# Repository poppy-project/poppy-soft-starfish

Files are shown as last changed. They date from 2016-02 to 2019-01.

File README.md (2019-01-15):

# Poppy Soft Starfish

This soft robot intergrates flexible silicon parts that can be easily design and built at a very low cost (>1$). It make use of the [poppy-soft-connector](https://github.com/poppy-project/poppy-soft-connector).

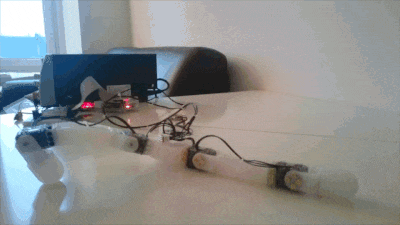
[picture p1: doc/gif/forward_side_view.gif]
forward_side_view


Discussions about this project are located at [this post](https://forum.poppy-project.org/t/poppy-soft-connector/2152). The project has been highlighted on [Hackaday](https://hackaday.com/2016/08/17/struggling-robot-made-with-diy-soft-limbs/)

## Principles 

By embedding hard connectors into silicon based parts, we create soft parts with a standard mechanical interface. These parts can be used as plug and play building blocks in our robots. See our [tutorial video](https://youtu.be/B3CZs55AJQo).

To create the soft part you have to prepare a mold of the desired shape. The mold's wall should be 2.2mm thick (for Ollo rivets) and include Ollo holes at the position you would like to add the connectors. The connectors are then positioned into the mold and maintained in place using Ollo rivet. You can then pour the polymer of your choice into the mold and allow for enough time for the polymer to cure - thus embedding the connector into the part. The soft part can then be unmolded and attached with XL-320 motors or any Ollo parts to create 'soft robots'. The starfish robot demonstrates how to use soft connectors.

The possibilities are immense as many different kinds of polymer can be used with many different properties. It also allows to embed electronics, sensors, cables, and more into the body of our robots. We hope this will tickle the imagination and open new possibilities for artistic minded people!

## More information

- [Tutorial video](https://youtu.be/B3CZs55AJQo)
- [doc folder](doc) for building instructions and help
- [hardware folder](hardware) for the mechanical parts
- [software folder](software) for code examples

### Contributing

Create your own soft robot and share it on [our forum](https://forum.poppy-project.org/)!

You can also propose new optimized design for the [poppy-soft-connector](https://github.com/poppy-project/poppy-soft-connector).

To contribute to this repository, you can [fork it](https://help.github.com/articles/fork-a-repo/) and issue a [pull request](https://help.github.com/articles/using-pull-requests/). [[Another useful link]](https://gun.io/blog/how-to-github-fork-branch-and-pull-request/)

### License

All the technological development work made in the Poppy project is freely available under open source licenses. Only the name usage *"Poppy"* is restricted and protected as an international trademark, please contact us if you want to use it or have more information.

| License | Hardware | Software |
| --- | :---: | :---: |
| Title  | [Creatives Commons BY-SA](http://creativecommons.org/licenses/by-sa/4.0/)  |[GPL v3](http://www.gnu.org/licenses/gpl.html)  |
| Logo  |   |GPL V3 (http://www.gnu.org/licenses/gpl.html)  |

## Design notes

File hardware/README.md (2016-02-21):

## Hardware

The parts have been design using [onshape](https://www.onshape.com/). The project has been made public at [this link](https://cad.onshape.com/documents/56af95b6e4b06a92e0eda720/w/a53eaed345df8e54532db1e2/e/a165c83ad81843f33ed38c05)
(Note: If the link does not work, run a search for ''Poppy Soft Robot XL320'')

The stl files are also available under [molds](molds) and [parts](parts).

Checkout the [BOM](BOM.md) to know how many of each to print.

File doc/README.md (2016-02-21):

## Building your robot

The complete bill of material is [here](BOM.md)

Video showcasing the building process are available:

- [Summary of all steps](https://youtu.be/B3CZs55AJQo)

- [Assembling the molds](https://youtu.be/NGw_e99sHJw)

- [Molding](https://youtu.be/pZrcofLqdRw)

- [Unmolding](https://youtu.be/WqsFyHN0t-A)

- [Assembling the robot](https://youtu.be/N8gOX-NB1fE)

Some demo code is available under the [software folder](https://github.com/poppy-project/poppy-soft-starfish/tree/master/software/poppy_soft_starfish), it implements the forward motion.

[[video_1]](https://youtu.be/_0Psq-BkSfY) [[video_2]](https://youtu.be/mUjL1PCE9o8) [[video_3]](https://youtu.be/N8iv0Vt9XzM)

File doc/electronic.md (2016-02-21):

# About the electronic

A small bit of electronic hacking is required for now. The cables between motors have two purposes:
- distribute alimentation to each motor
- convey messages to each motor (ordering them to move or asking them for sensors' values)

First, you will need a hub for connecting all arms together on the same communication and power bus.

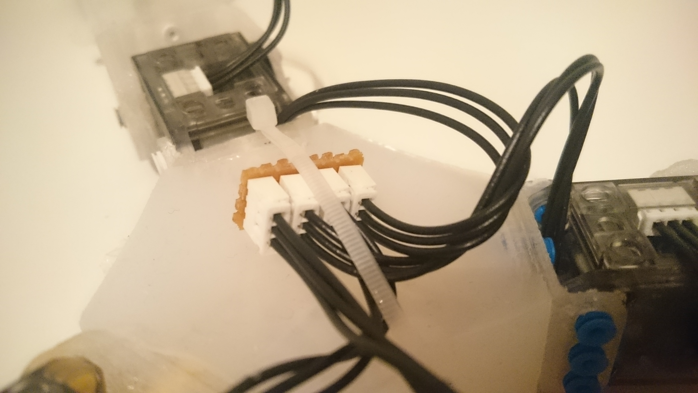
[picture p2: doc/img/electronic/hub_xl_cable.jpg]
Hub


Then you need to power the Xl320 motors with 7.5V. Thus the alimentation should be added between the USB2Dynamixel (that deals with communication aspects) and the motors. To this end simply create the following hack.

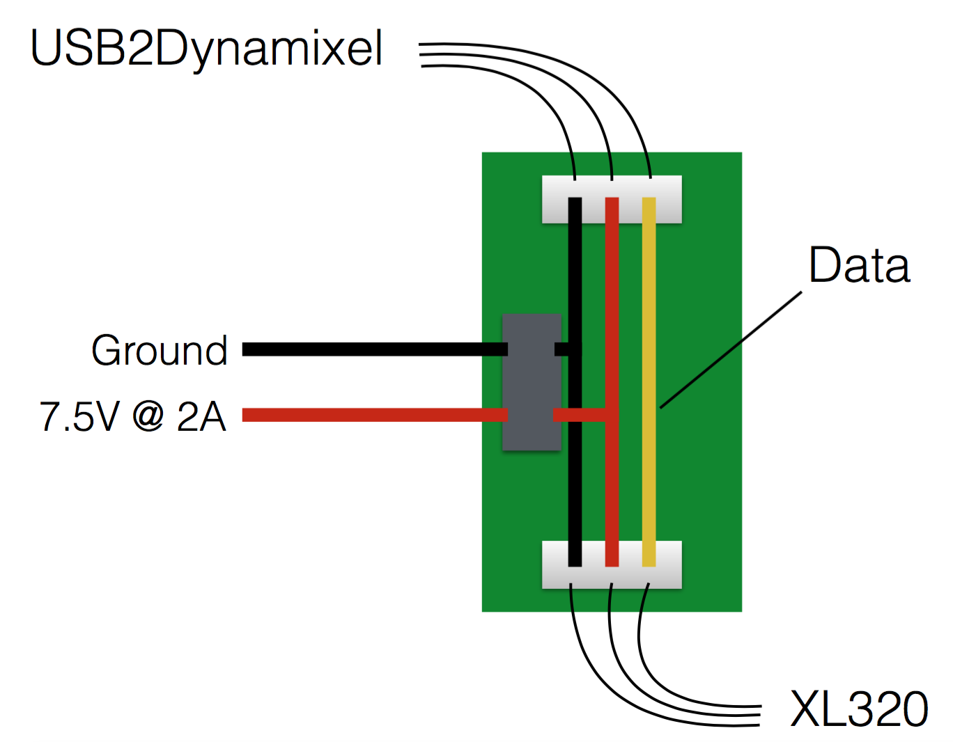
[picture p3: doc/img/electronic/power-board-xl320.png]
Power Board


Then connect the USB2Dynamixel on one end and the first motor on the other end. Connect the USB2Dynamixel to your computer or Raspberry Pi. And power the board with 7.5V.

The communication with the motor is TTL, thus configure the USB2Dynamixel in TTL mode as shown below.

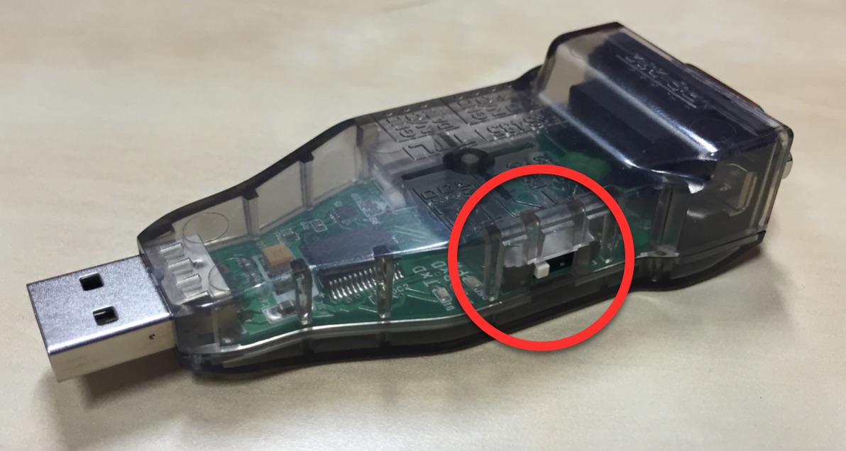
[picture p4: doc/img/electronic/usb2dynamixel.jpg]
USB2Dynamixel


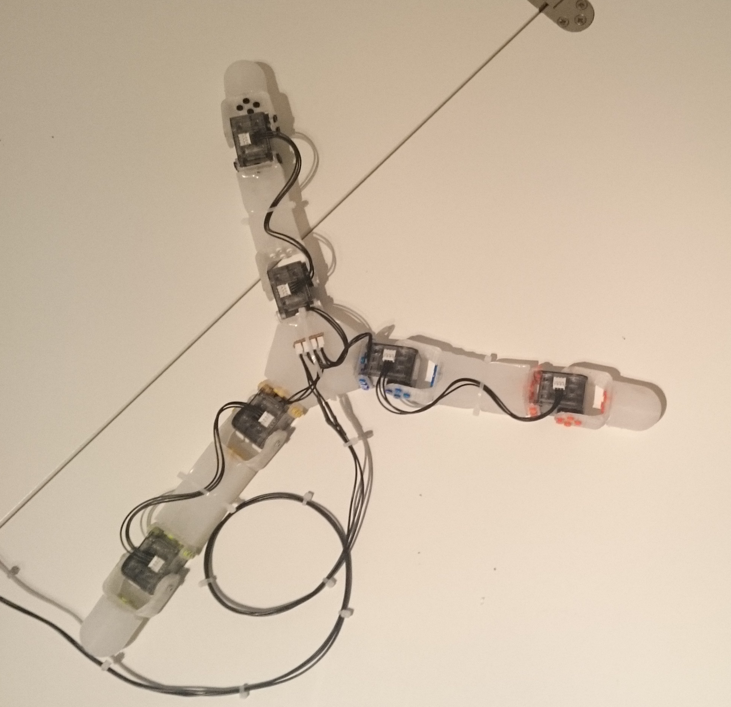
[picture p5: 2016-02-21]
doc/img/full_robot.jpg

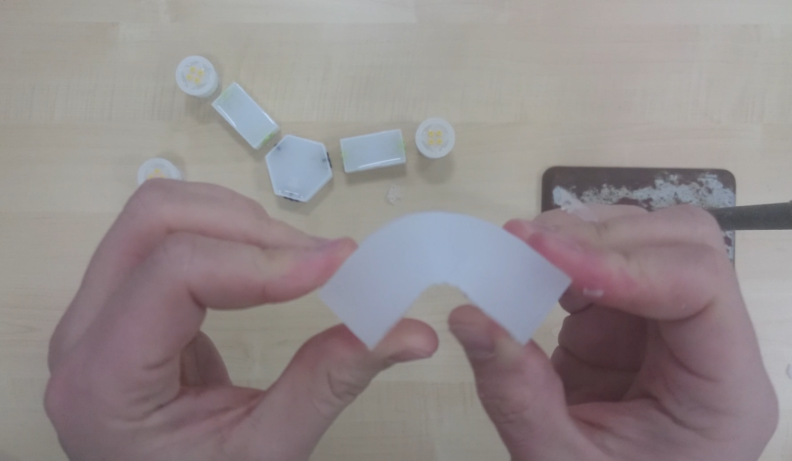
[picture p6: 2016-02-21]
doc/img/unmold.png

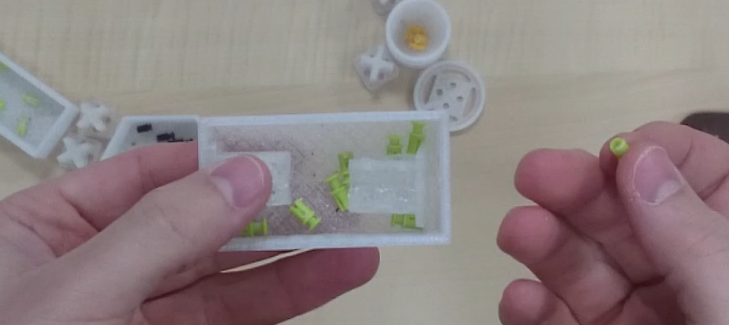
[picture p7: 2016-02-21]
doc/img/prepare_mold.png

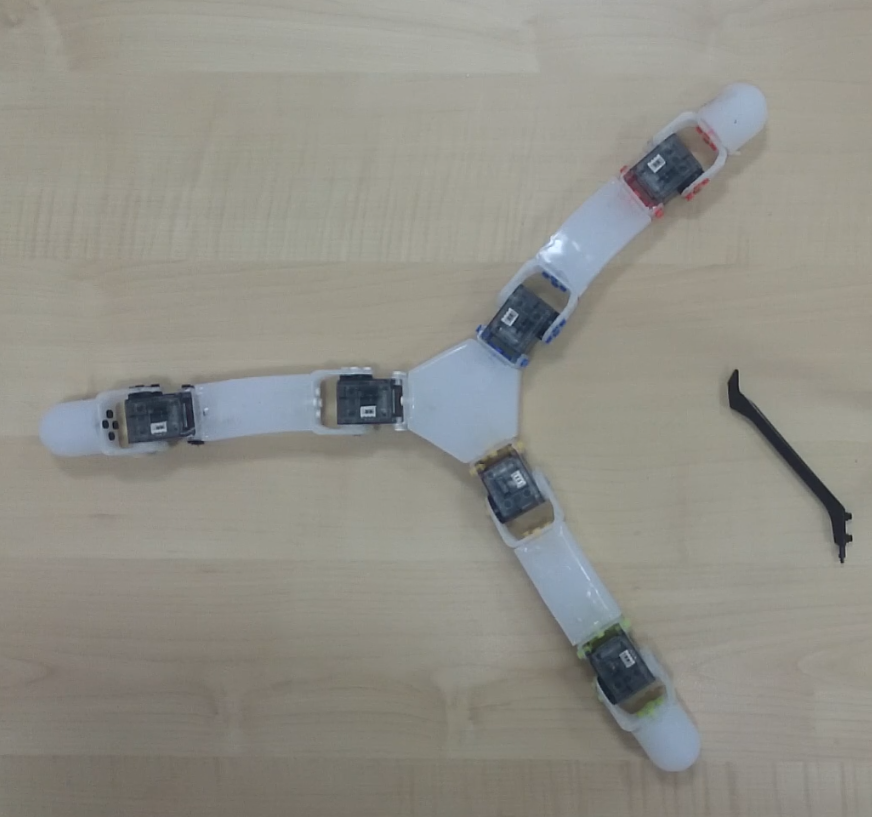
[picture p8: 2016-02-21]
doc/img/built.png

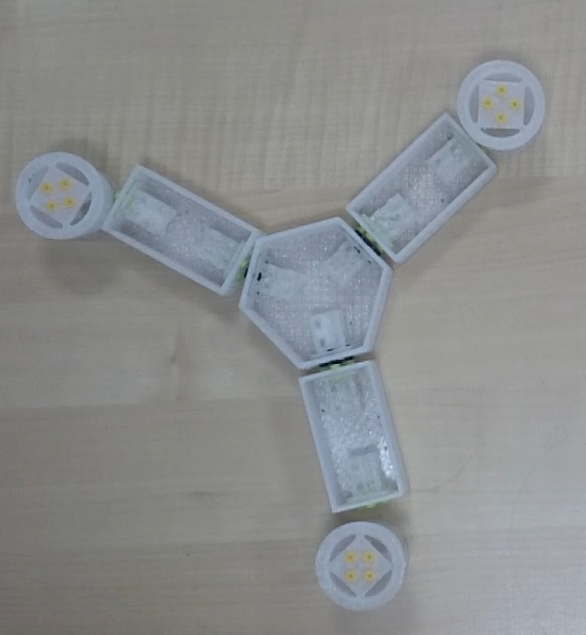
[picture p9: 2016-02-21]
doc/img/mold_ready.png

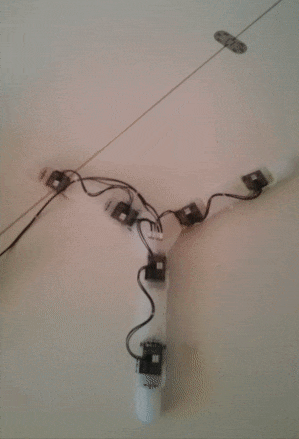
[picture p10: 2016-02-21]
doc/gif/forward_top_view.gif

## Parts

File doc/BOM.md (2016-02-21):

## BOM

For building a Poppy Soft Starfish, you will need:

* the 3D printed parts: [[STL]](https://github.com/poppy-project/poppy-soft-starfish/tree/master/hardware) [[BOM]](https://github.com/poppy-project/poppy-soft-starfish/blob/master/hardware/BOM.md)

* some silicone, we used the [Ecoflex 00-30](http://www.smooth-on.com/Silicone-Rubber-an/c2_1115_1130/index.html)

* 6x Robotis [XL-320](http://www.generationrobots.com/en/401692-dynamixel-xl-320-servo-motor.html?search_query=OLLO&results=23)
* 7x [XL cables](http://www.generationrobots.com/en/402091-3p-190-mm-cables-for-xl-servos-x5.html) (of which 1 longer for connecting to the electronics and allow some movement)

* many [OLLO rivets](http://www.generationrobots.com/en/401870-ollo-rivet-set-ors-10.html) (between 4 and 12 per motor)
* 1x [OLLO Tool](http://www.generationrobots.com/en/401872-ollo-tool.html)

* 1x [Raspberry Pi 2](https://www.raspberrypi.org/raspberry-pi-2-on-sale/) with its power supply

* 1x [USB2Dynamixel](http://www.generationrobots.com/en/400848-usb2dynamixel-robotis.html?search_query=usb2dynamixel&results=20)

* 1x [TTL cable](http://www.generationrobots.com/en/401739-3p-cable-set-bcs-3p01-for-dynamixel-servo-motors.html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)

* 1 external power supply able to output 7.5V at least 2A for the motors (see [here](https://forum.poppy-project.org/t/birth-of-poppyergojr-and-support-for-low-cost-xl-320-motors/1052/10) for details)

* 1x small electronic board (see the [electronic section](electronic.md))

* 1x 4 way hub for XL cables (see the [electronic section](electronic.md))

*All the links to products we provide are from our local distributor but feel free to choose your own.*

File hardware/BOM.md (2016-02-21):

## Molds

| Part Name | Quantity | Note |
| ---:|:---:|:---:|
| straight_large_mold | 3 |  |
| three_way_mold | 3 |  |
| feet_mold | 3 |  |
| feet_top_mold | 3 |  |

Depending on the time you have, one mold of each type is enough as they can be reused.

## Parts

| Part Name | Quantity | Note |
| ---:|:---:|:---:|
| soft_connector | 12 |  |
| short_U | 6 |  |
| long_U | 6 |  |

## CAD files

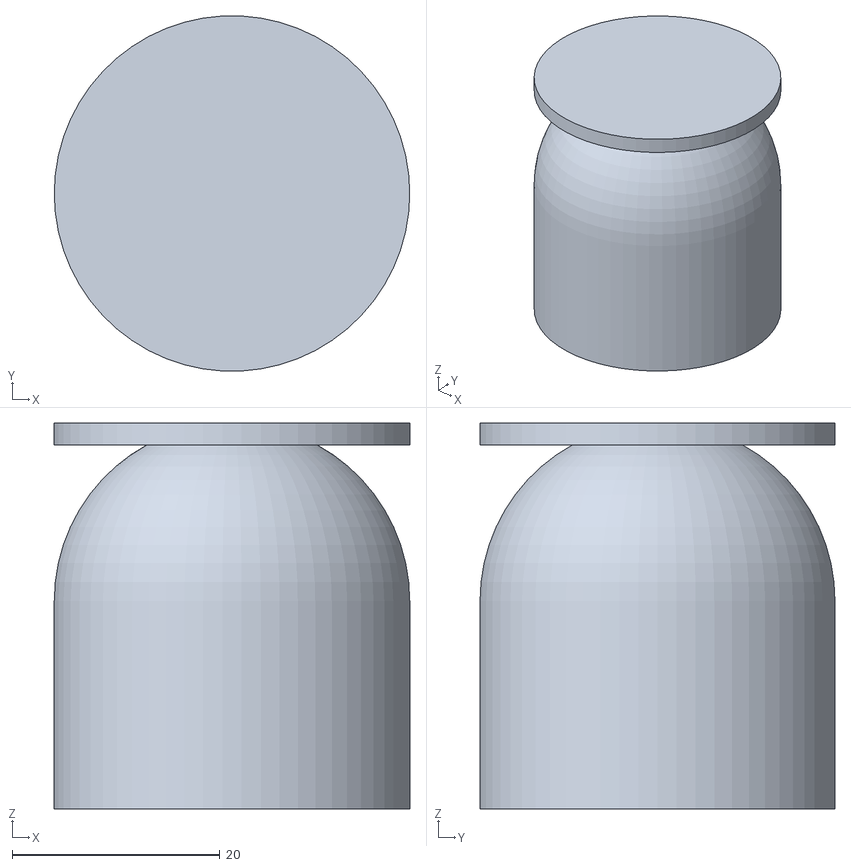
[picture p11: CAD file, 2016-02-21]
hardware/molds/feet_mold.stl
34.2 x 34.1 x 37.1

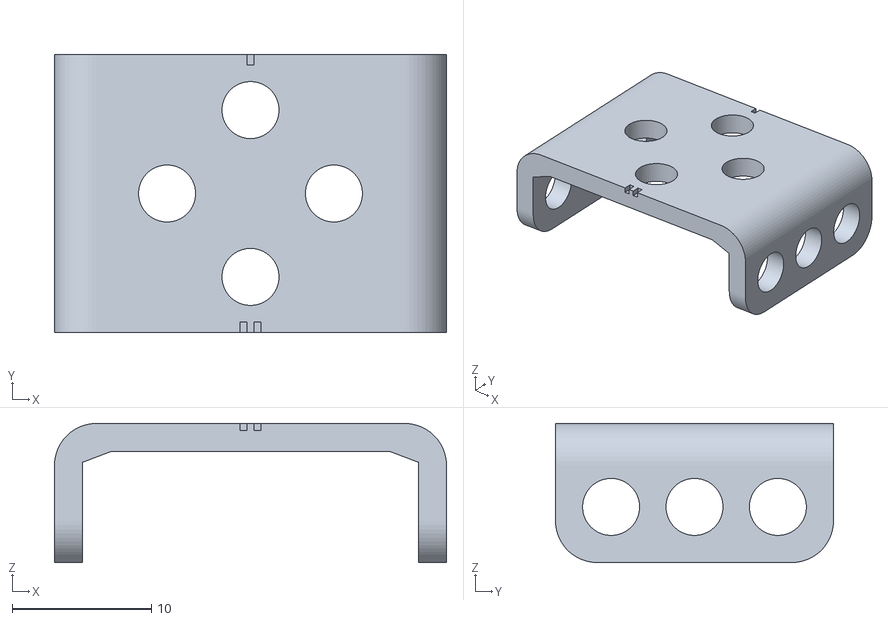
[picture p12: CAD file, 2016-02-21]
hardware/parts/short_U.stl
28.2 x 20.0 x 10.0

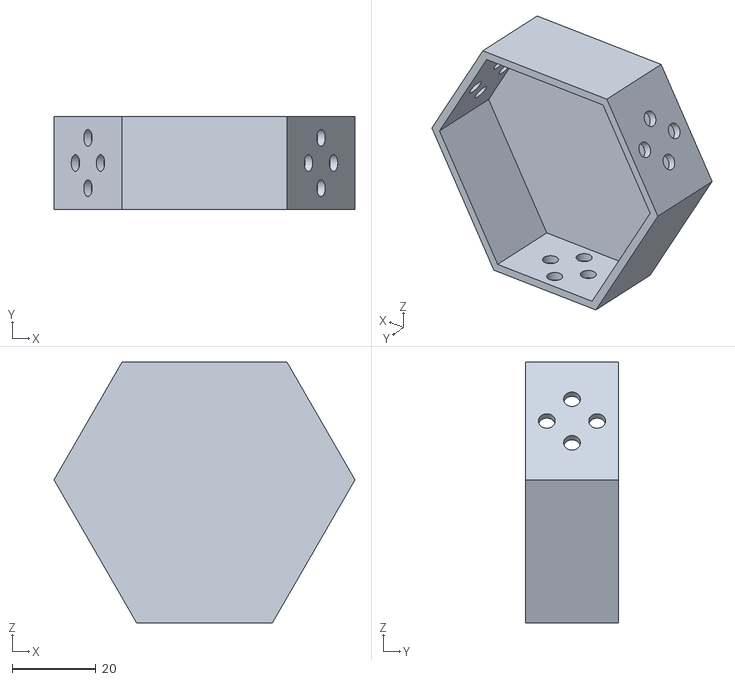
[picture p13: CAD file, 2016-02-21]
hardware/molds/three_way_mold.stl
71.8 x 22.1 x 62.2

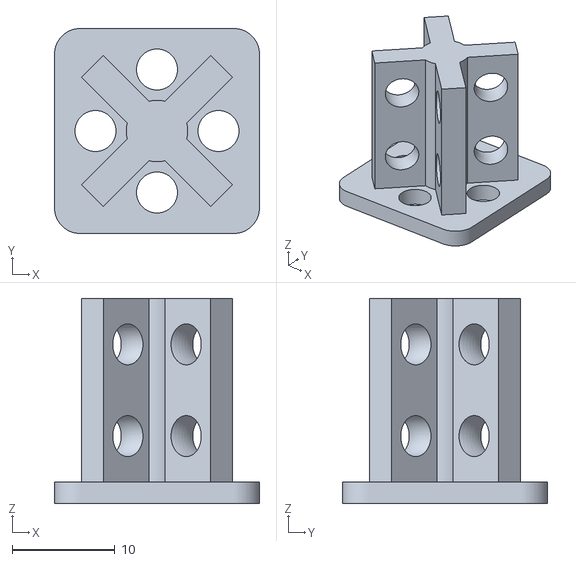
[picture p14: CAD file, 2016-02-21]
hardware/parts/soft_connector.stl
20.0 x 20.0 x 20.0

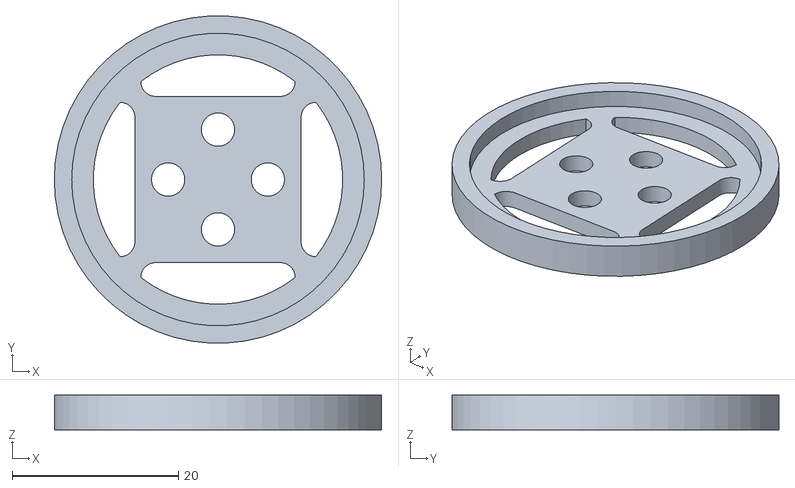
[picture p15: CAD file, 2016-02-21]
hardware/molds/feet_top_mold.stl
39.4 x 39.3 x 4.20

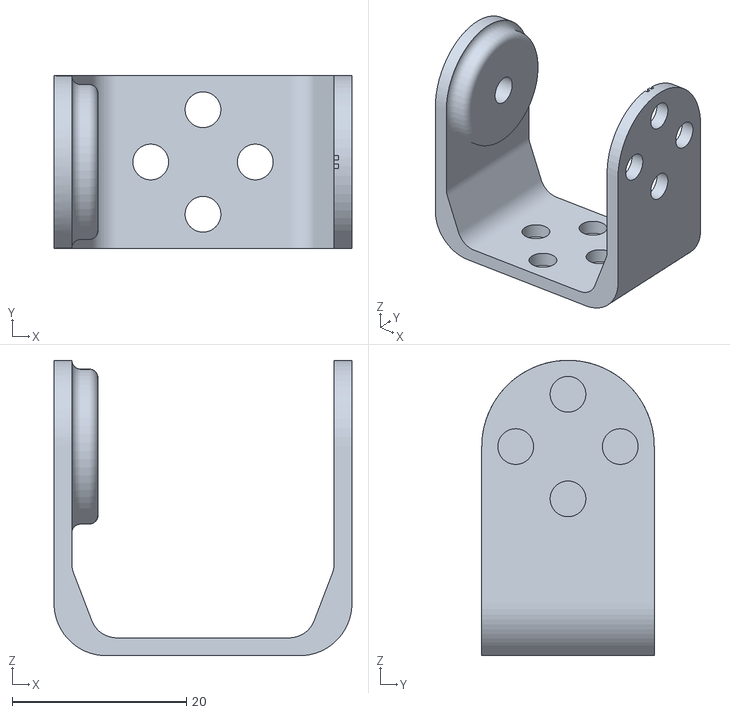
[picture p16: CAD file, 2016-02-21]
hardware/parts/long_U.stl
34.2 x 19.8 x 33.9

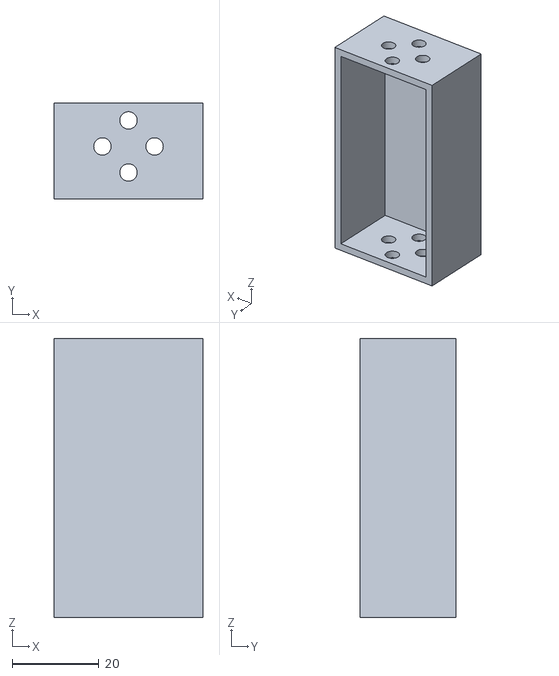
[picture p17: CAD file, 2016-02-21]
hardware/molds/straight_large_mold.stl
34.2 x 22.1 x 64.2

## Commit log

2016-02-20 motorgroups in config
2016-02-21 added stl files
    [feet_mold.stl, feet_top_mold.stl, long_U.stl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]

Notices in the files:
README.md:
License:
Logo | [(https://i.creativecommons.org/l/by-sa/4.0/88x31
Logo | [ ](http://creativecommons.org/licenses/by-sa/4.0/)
